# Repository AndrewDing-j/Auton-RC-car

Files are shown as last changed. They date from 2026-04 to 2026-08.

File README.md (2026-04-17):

# Auton-RC-car
## An autonomous car powered by Raspberry Pi 5 and Arduino Nano 33 BLE Sense which can navigate through roads of various width that are flanked by walls.

### Why this project?
I have always been interested in computer vision and found that this was a great excuse to make a project centred on that. Automation facinates me and I am very aware of how the world is rapidly moving towards self-driving vehicles through autonomous taxi services. I wanted to try my own hand in building something similar while also building the skills that could help me contribute to a better, more sustainable future.

### Software:
The Raspberry Pi is responsible for processing environmental data, while the Arduino serves as the controller for most peripherals, excluding the camera, and handles IMU information.
Uses a simple command protocol which allows the Arduino and Raspberry Pi to communicate with one another and interpret several commands.

### Hardware:
The chassis is that of a WL Toys K989 1:28 Scale Rally Car. All components - except for the suspension springs, wheels, bumper, and a majority of the steering mechanism - have been removed or replaced with 3DP parts.





**Current main features include:**
---------------------------------------------------------------------
- **Auckerman Steering** (Comes as a part of the chassis and I could not find the details that would allow me to make a CAD of it)
- - Enables sharper turns
- - Smoother steering
- - Greater control at low speeds
- - Reduced tire scrubbing
- **Wide-angle Pi 5 Camera (CSI interface, 130+ FOV)**
- - Wide FOV for wall detection
- - Inexpensive, so easily replacable
- - 4K resolution
- **Raspberry Pi 5**
- - Handles visual data from camera
- - Processes visual information with the help of a Python script utilizing OpenCV
- - Reacts to the environment and sends commands to an Arduino Nano based on the data recieved
- - Generally handles driving in two states: "STRAIGHT" and "TURN"
- **Yahboom PSU Expansion Board for Raspberry Pi 5**
- - Provides stable power to Raspberry Pi 5
- - Indirectly powers Arduino Nano through Raspberry Pi 5
- - Supplied with a 2 cell 1300mAh LiPo Gens Ace battery
- **Arduino Nano 33 BLE Sense**
- - Compact
- - Controls motors and servos
- - Returns IMU gyroscopic data
- - Runs callibration script to counteract the IMU's gyroscopic drift
- - Handles commands



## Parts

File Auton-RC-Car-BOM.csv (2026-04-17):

Item | Quantity | Description
WL Toys K989 1:28 Scale Rally Car (RTR) | 1 | Contains aluminum 1:28 sclae RC car chassis. Wheels attached.
8MP Camera for Raspberry Pi 5 IMX219 130° FOV CSI Interface with 15 cm FFC for RPI 5 Zero/ZeroW/2W | 1 | 130 Degree wide camera with 8MP/4K resolution. Captures visual information so the Raspberry Pi 5 can send appropriate commands to the Arduino module.
Yahboom Power supply Expansion Board for Raspberry Pi 5 (5V/5A, ideally USB PD power supply) | 1 | Provides a regulated 5.0V source of power to the Raspberry Pi 5.
LiPo battery | 1 | Rechargeable Gens Ace 2 cell 1300mAh 7.4v battery with a female dean connector. Serves as the main power source.
Button (to start the robot) | 1 | Button to power the RC Car on and off.
Arduino Nano 33 BLE Sense Rev2 | 1 | Arduino Nano module with an on board IMU. Requires 3.3v power supply. Will control the peripheries which move the RC Car
Hitec HS-5055MG Servo Motor | 1 | 11.9g metal gear digital microservo. Steers the car and controlled by the Arduino module through the Lizard Pro Esc.
Furitek Lizard Pro 30A/50A Brushed/Brushless Esc For Axial SCX24 With FOC Technology | 1 | Esc with controls for BLDC motor and servo. Can recieve and redistribute power.
BLDC Motor | 1 | 17.5g BLDC micro motor with an rpm of 3450/KV. Will provide speed for the motor and controlled through the Esc.
Main Platform | 1 | 3DP platform with holes for the Arduino, Raspberry Pi, and other 3DP components.
Battery Mount | 1 | 3DP Platform to maintain the LiPo battery in a central area.
Camera Mount | 1 | 3DP frame structure with holes drilled at the top to screw on the 8MP Camera. Attaches to the Raspberry Pi 5 with pegs.
Motor Holder/Gearbox | 1 | 3DP gerabox that keeps the BLDC motor stable and in place.
Wheel Clamp | 2 | 3DP piece that keeps suspensions springs and bottom of wheels from going above the chassis.
Steering Rod | 1 | 3DP steering rod attached to the wheels and servo.

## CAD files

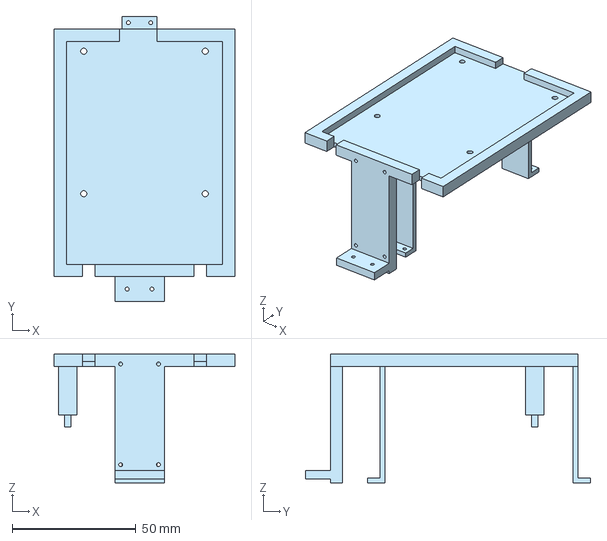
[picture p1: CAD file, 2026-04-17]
3DP/Main Platform.step
73.0 x 115.0 x 52.0 mm

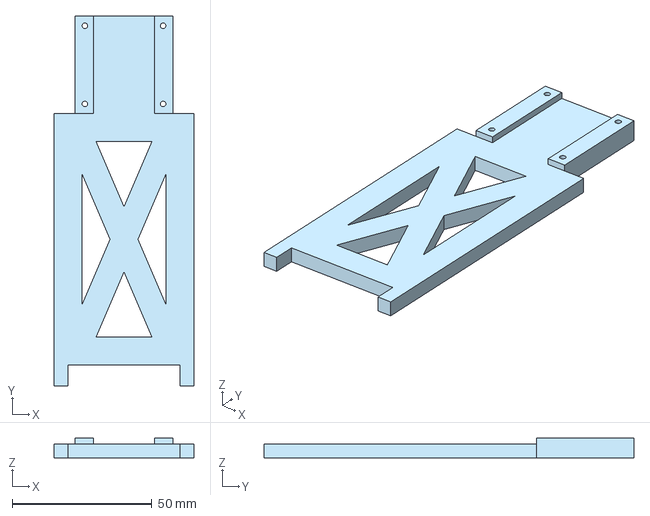
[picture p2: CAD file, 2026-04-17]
3DP/Camera Mount.step
50.0 x 132.5 x 7.10 mm

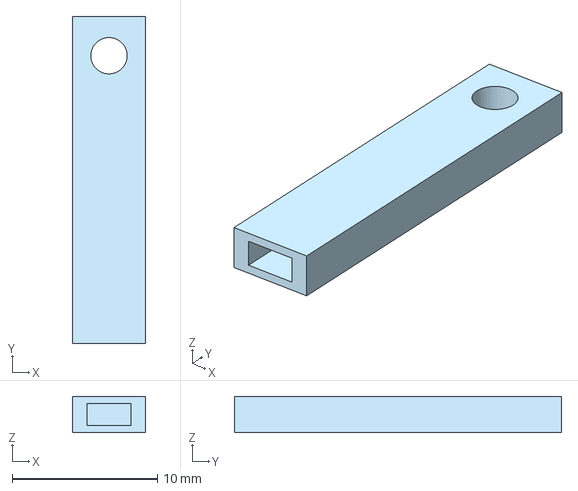
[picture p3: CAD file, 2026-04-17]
3DP/Bottom part 1.step
5.00 x 22.5 x 2.50 mm

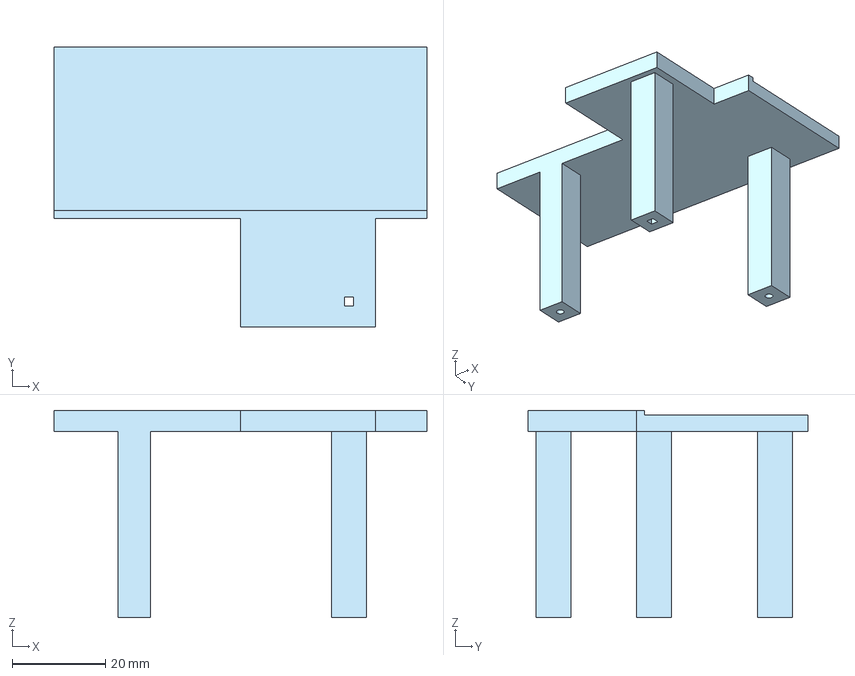
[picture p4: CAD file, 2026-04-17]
3DP/Battery Mount.step
80.0 x 60.0 x 44.5 mm

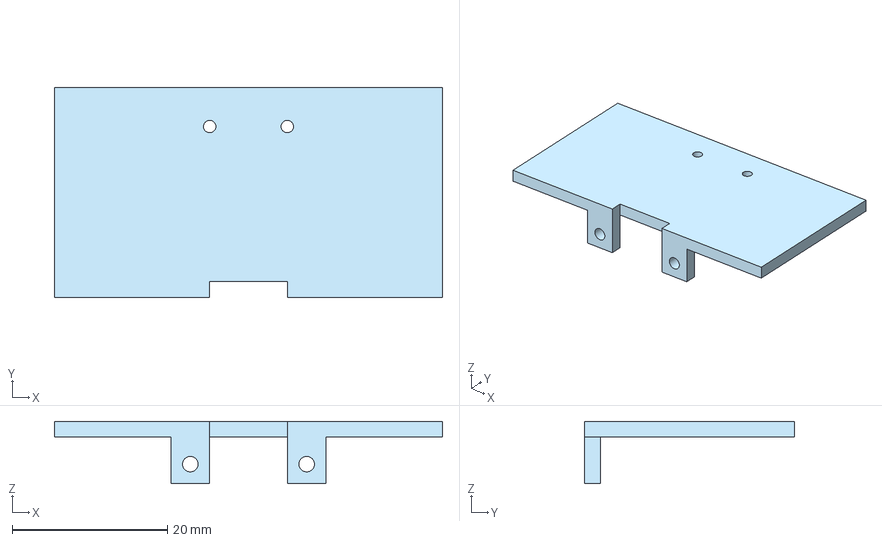
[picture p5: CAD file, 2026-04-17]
3DP/Wheel clamp.step
50.0 x 27.0 x 8.00 mm

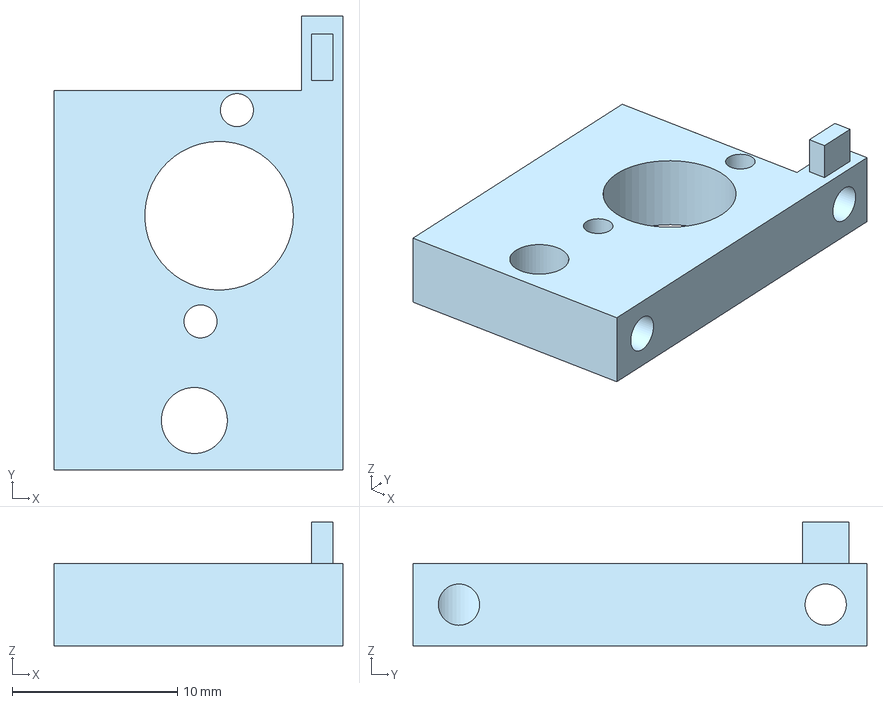
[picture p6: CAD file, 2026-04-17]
3DP/Gearbox.step
17.5 x 27.5 x 7.50 mm

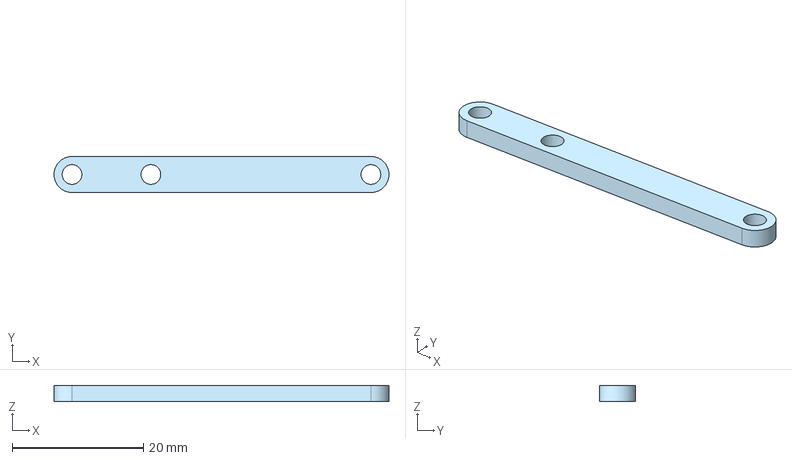
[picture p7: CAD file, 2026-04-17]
3DP/Steering Rod.step
51.0 x 5.50 x 2.50 mm

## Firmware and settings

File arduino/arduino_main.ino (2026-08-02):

#include <Arduino.h>
#include <ctype.h>
#include <string.h>
#include <stdlib.h>
#include <Servo.h>
#include <Arduino_BMI270_BMM150.h>

static float q0=1, q1=0, q2=0, q3=0;
static float eIx=0, eIy=0, eIz=0;
static unsigned long lastTime = 0;
static float gbx=0, gby=0, gbz=0;

// reference quaternion everything is relative to this after zeroing
static float r0=1, r1=0, r2=0, r3=0;

// cached mag updated only when new data arrives, used every frame
static float cachedMx=0, cachedMy=0, cachedMz=0;

static const size_t MAX_LINE = 16;  // Max command line length, excluding EOL
static char lineBuf[MAX_LINE + 1];
static size_t lineLen = 0;
static const char SOC = '$';  // start of command character
static bool inCommand = false;
static float biasX = 0.0, biasY = 0.0, biasZ = 0.0;
Servo servo;
Servo motor;
#define SERVO_PIN 8
#define MOTOR_PIN 9

// This need to be calibrated board to board. Please uncomment calibrateMag() under void loop to do so.
#define MAG_X_OFFSET  39.0f
#define MAG_Y_OFFSET  30.0f
#define MAG_Z_OFFSET  13.5f

// Kp = how fast it corrects, Ki = slowly kills gyro bias
#define Kp  2.0f
#define Ki  0.05f

static float heading = 0.0f;

void calibrateGyro() {
  Serial.println("Keep still — calibrating gyro...");
  float sx=0, sy=0, sz=0;
  int n = 2000;
  for (int i=0; i<n; i++) {
    float gx,gy,gz;
    while (!IMU.gyroscopeAvailable());
    IMU.readGyroscope(gx,gy,gz);
    sx+=gx; sy+=gy; sz+=gz;
    delay(3);
  }
  gbx=sx/n; gby=sy/n; gbz=sz/n;
  Serial.print("Gyro bias: ");
  Serial.print(gbx,4); Serial.print(" ");
  Serial.print(gby,4); Serial.print(" ");
  Serial.println(gbz,4);
}

// run once, rotate board in all directions 30s, paste offsets above
void calibrateMag() {
  Serial.println("Rotate board in all directions for 30s...");
  float xmin=1e9,xmax=-1e9,ymin=1e9,ymax=-1e9,zmin=1e9,zmax=-1e9;
  unsigned long start = millis();
  while (millis()-start < 30000) {
    if (!IMU.magneticFieldAvailable()) continue;
    float mx,my,mz;
    IMU.readMagneticField(mx,my,mz);
    xmin=min(xmin,mx); xmax=max(xmax,mx);
    ymin=min(ymin,my); ymax=max(ymax,my);
    zmin=min(zmin,mz); zmax=max(zmax,mz);
    delay(10);
  }
  Serial.println("Done! Paste these into your #defines:");
  Serial.print("#define MAG_X_OFFSET  "); Serial.println((xmin+xmax)/2, 4);
  Serial.print("#define MAG_Y_OFFSET  "); Serial.println((ymin+ymax)/2, 4);
  Serial.print("#define MAG_Z_OFFSET  "); Serial.println((zmin+zmax)/2, 4);
  while(1);
}

void mahonyUpdate(float ax, float ay, float az,
                  float gx, float gy, float gz,
                  float mx, float my, float mz, float dt) {
  float norm;

  norm = sqrtf(ax*ax+ay*ay+az*az);
  if (norm == 0) return;
  ax/=norm; ay/=norm; az/=norm;

  norm = sqrtf(mx*mx+my*my+mz*mz);
  if (norm == 0) return;
  mx/=norm; my/=norm; mz/=norm;

  float hx = 2*(mx*(0.5f-q2*q2-q3*q3) + my*(q1*q2-q0*q3) + mz*(q1*q3+q0*q2));
  float hy = 2*(mx*(q1*q2+q0*q3) + my*(0.5f-q1*q1-q3*q3) + mz*(q2*q3-q0*q1));
  float bx = sqrtf(hx*hx+hy*hy);
  float bz = 2*(mx*(q1*q3-q0*q2) + my*(q2*q3+q0*q1) + mz*(0.5f-q1*q1-q2*q2));

  float vx = 2*(q1*q3-q0*q2);
  float vy = 2*(q0*q1+q2*q3);
  float vz = q0*q0-q1*q1-q2*q2+q3*q3;
  float wx = 2*(bx*(0.5f-q2*q2-q3*q3) + bz*(q1*q3-q0*q2));
  float wy = 2*(bx*(q1*q2-q0*q3)       + bz*(q0*q1+q2*q3));
  float wz = 2*(bx*(q0*q2+q1*q3)       + bz*(0.5f-q1*q1-q2*q2));

  float ex = (ay*vz-az*vy) + (my*wz-mz*wy);
  float ey = (az*vx-ax*vz) + (mz*wx-mx*wz);
  float ez = (ax*vy-ay*vx) + (mx*wy-my*wx);

  eIx += Ki*ex*dt;
  eIy += Ki*ey*dt;
  eIz += Ki*ez*dt;

  gx += Kp*ex + eIx;
  gy += Kp*ey + eIy;
  gz += Kp*ez + eIz;

  gx *= DEG_TO_RAD;
  gy *= DEG_TO_RAD;
  gz *= DEG_TO_RAD;

  float dq0 = 0.5f*(-q1*gx-q2*gy-q3*gz)*dt;
  float dq1 = 0.5f*( q0*gx+q2*gz-q3*gy)*dt;
  float dq2 = 0.5f*( q0*gy-q1*gz+q3*gx)*dt;
  float dq3 = 0.5f*( q0*gz+q1*gy-q2*gx)*dt;

  q0+=dq0; q1+=dq1; q2+=dq2; q3+=dq3;

  norm = sqrtf(q0*q0+q1*q1+q2*q2+q3*q3);
  q0/=norm; q1/=norm; q2/=norm; q3/=norm;
}

void readAndFuse(float dt) {
  // update mag cache only when fresh data is ready (it's slow ~10Hz)
  if (IMU.magneticFieldAvailable()) {
    float mx,my,mz;
    IMU.readMagneticField(mx,my,mz);
    // BMI270 rotated 90deg on board + align to same frame
    cachedMx =  my - MAG_X_OFFSET;
    cachedMy = -mx - MAG_Y_OFFSET;
    cachedMz = -mz - MAG_Z_OFFSET;
  }

  // always run filter at full speed with last known mag
  if (!IMU.accelerationAvailable() || !IMU.gyroscopeAvailable()) return;

  float ax,ay,az,gx,gy,gz;
  IMU.readAcceleration(ax,ay,az);
  IMU.readGyroscope(gx,gy,gz);
  gx -= gbx; gy -= gby; gz -= gbz;

  float rax=-ax, ray=ay, raz=az;
  float rgx=-gx, rgy=gy, rgz=gz;

  mahonyUpdate(rax,ray,raz, rgx,rgy,rgz, cachedMx,cachedMy,cachedMz, dt);
}

void warmupAndZero() {
  Serial.println("Warming up — keep still...");

  // seed the mag cache before warmup starts
  while (!IMU.magneticFieldAvailable());
  float mx,my,mz;
  IMU.readMagneticField(mx,my,mz);
  cachedMx =  my - MAG_X_OFFSET;
  cachedMy = -mx - MAG_Y_OFFSET;
  cachedMz = -mz - MAG_Z_OFFSET;

  unsigned long start = millis();
  lastTime = micros();
  while (millis()-start < 3000) {
    unsigned long now = micros();
    float dt = (now-lastTime)*1e-6f;
    if (dt < 0.002f) continue;
    lastTime = now;
    if (dt > 0.05f) dt = 0.05f;
    readAndFuse(dt);
  }

  // store inverse of settled quaternion so all angles are relative to startup pose
  r0= q0; r1=-q1; r2=-q2; r3=-q3;
  Serial.println("Zeroed. Go!");
}

void startupCalibration() {
  calibrateGyro();
  warmupAndZero();
  lastTime = micros();
  heading = 0.0f;
}

static void processCommand(char* cmd, float heading=heading) {
  if (!cmd || cmd[0] == '\0') return;

  char* cr = strchr(cmd, '\r');
  if (cr) *cr = '\0';

  while (*cmd && isspace((unsigned char)*cmd)) cmd++;  // Trim leading whitespace
  if (*cmd == '\0') return;

  char type = *cmd++;

  // Parse int argument
  char* endp = nullptr;
  long val = strtol(cmd, &endp, 10);

  if (type == 'C') {  // (re-)calibrate gyro and zero heading
      startupCalibration();
  } else if (type == 'S') {                            // Set servo position
      if (val < 25 || val > 130) return;  // Invalid angle
      //Serial.println(val);
      servo.write(val);
  } else if (type == 'M') {  // return IMU data and turn
    if (val < 1000 || val > 2000) return;  // Invalid speed
    motor.writeMicroseconds(val);
    //Serial.println(val);
  } else if (type == 'L') {
    if (val < 22 || val > 24) return;  // Invalid LED
    digitalWrite(22, LOW);
    digitalWrite(23, LOW);
    digitalWrite(24, LOW);
    digitalWrite(val, HIGH);
  } else if (type == 'I') {
    Serial.println(heading);
  }
}

void setup() {
  pinMode(22, OUTPUT); // blue
  pinMode(23, OUTPUT); // red
  pinMode(24, OUTPUT); // green

  servo.attach(SERVO_PIN, 900, 2100);
  motor.attach(MOTOR_PIN, 1000, 2000);
  servo.write(80);
  motor.writeMicroseconds(1500);

  Serial.begin(115200);
  while (!Serial);

  if (!IMU.begin()) {
    Serial.println("Failed to initialize IMU!");
    while (1);
  }
  Serial.println("IMU initialized successfully.");

  // uncomment once to get mag offsets, paste above, then comment out again
  //calibrateMag();

  startupCalibration();
}

void loop() {
  // CMD Processing
  if (Serial.available() > 0) {
    char c = (char)Serial.read();
    if (c == SOC) {
      inCommand = true;
      lineLen = 0;
    }
    else if (inCommand) {
      if (c == '\n') {
        lineBuf[lineLen] = '\0';  // Null-terminate command
        processCommand(lineBuf, heading);
        inCommand = false;
        lineLen = 0;
      } else if (lineLen < MAX_LINE) {
        lineBuf[lineLen++] = c;  // Append char to command buffer
      } else {
        // Command too long
        inCommand = false;
        lineLen = 0;
      }
    }
  }

  //IMU Background Processing
  if (IMU.gyroscopeAvailable()) {
    float x, y, z;
    IMU.readGyroscope(x, y, z);
    z -= gbz;

    if (abs(z) < 0.1) z = 0.0;  // ignores insignificant gyro readings/noise
      
    unsigned long now = micros();
    float dt = (now-lastTime)*1e-6f;  // calc dt (elapsed time)
    lastTime = now;

    heading -= dt * z;  // integrate gyro's angular velocity to get heading
  }
}

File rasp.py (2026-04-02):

import time, serial, cv2, numpy as np
from picamera import PiCamera
from time import sleep

# Camera init
picam2 = PiCamera()
picam2.preview_configuration.main.size = (640, 480)
picam2.preview_configuration.main.format = "RGB888"
picam2.preview_configuration.controls.FrameRate = 30
picam2.preview_configuration.align()
picam2.configure("preview")
picam2.start()
sleep(2) # Let the camera warm up

ser = serial.Serial('/dev/ttyACM0', 112500, timeout=1) # Update with your Arduino's port
ser.reset_input_buffer() # Clear any pending data
ser.reset_output_buffer()

# Define ROIs (x1, y1, x2, y2)
roi1 = [20, 170, 240, 220] # Left side
roi2 = [400, 170, 620, 220] # Right side

def drawRoi(img, roi, color=(0, 255, 0), thickness=2, label=None):
    # Draws a rectangle on the image to indicate the ROI.
    x1, y1, x2, y2 = roi
    cv2.rectangle(img, (x1, y1), (x2, y2), color, thickness)
    if label:
        cv2.putText(img, label, (x1, max(15, y1 - 8)), 
                    cv2.FONT_HERSHEY_SIMPLEX, 1, color, 2, cv2.LINE_AA)
    return img

def wallAreaLab(frameRgb, roi, LabLower, LabUpper, minContour = 50):
    # Calculate percentage of pixels withing the Lab range in the ROI
    x1, y1, x2, y2 = roi
    roiImg = frameRgb[y1:y2, x1:x2]
    roiLab = cv2.cvtColor(roiImg, cv2.COLOR_RGB2Lab)
    roiLab = cv2.GaussianBlur(roiLab, (7,7), 0) # larger kernel = more smoothing
    mask = cv2.inRange(roiLab, LabLower, LabUpper)

    #noice cleanup
    kernel = np.ones((5,5), np.uint8)
    mask = cv2.morphologyEx(mask, cv2.MORPH_OPEN, kernel, iterations=1)
    mask = cv2.morphologyEx(mask, cv2.MORH_CLOSE, kernel, iterations=2)

    contours, _ = cv2.findContours(mask, cv2.RETR_EXTERNAL, cv2.CHAIN_APPROX_SIMPLE)
    areaMax = 0
    contourMax = None
    for c in contours:
        area = cv2.contourArea(c)
        if area >= minContour and area > areaMax:
            areamax = area
            contourMax = c
    if contourMax is not None:
        contourMax += [x1, y1] #shift contour points to full-frame coordinates
    return areaMax, contourMax, mask

def pidController(error, prevError, kp=0.1, ki=0.01, kd=0.05):
    global integral, prevError
    integral += error
    correction = kp * error + ki * integral + kd * (error - prevError)
    prevError = error
    return correction

# Define thresholds
LAB_LOWER = np.array([20,120,120], dtype=np.uint8) #adjust LAB_LOWER and LAB_UPPER based on the wall colour
LAB_UPPER = np.array([70,255,255], dtype=np.uint8)
ENTER_TURN_THRESH = 550
EXIT_TURN_THRESH = 1200
EXIT_TIME_THRESH = 5.0
EXIT_ANGLE_THRESH = 85.0

# Trigger protection
CONFRIM_FRAMES = 5  # Number of consecutive frames required to confirm a turn
side = None
confirmCount = 0
turnTime = None

# Turning variables
enterTurnDegree = None
turningDegree = None
turnsCompleted = 0

# PID variables
prevError = 0
integral = 0

mode = "STRAIGHT" #STRAIGHT, TURNING

# --- Main loop --- #
while True:
    frame = picam2.capture_array()
    now = time.monotonic()

    leftContour, leftMask, leftArea = wallAreaLab(frame, roi1, LAB_LOWER, LAB_UPPER)
    rightContour, rightMask, rightArea = wallAreaLab(frame, roi2, LAB_LOWER, LAB_UPPER)

    # --- State Machine --- #
    if mode == "STRAIGHT":
        ser.write(f"$S{pidController(leftArea-rightArea)}\n")
        if leftArea < ENTER_TURN_THRESH or rightArea < ENTER_TURN_THRESH:
            confirmCount += 1
        else:
            confirmCount = 0
        
        if confirmCount >= CONFIRM_FRAMES:
            if leftArea < rightArea:
                side = "LEFT"
            else:
                side = "RIGHT"
            confirmCount = 0
            mode = "TURNING"
            turnTime = now
            enterTurnDegree = int(ser.readline().decode().strip()) # Read current degree from Arduino's IMU
    
    elif mode == "TURNING":
        delta = abs(enterTurnDegree - int(ser.readline().decode()).strip())
        turningDegree = min(delta, 360 - delta) # handling of wrapping from 0 to 360 degrees
        elapsed = now - (turnTime if turnTime else now)
        if elasped > EXIT_TIME_THRESH and turningDegree > EXIT_ANGLE_THRESH:
            if (leftArea > EXIT_TURN_THRESH and side == "LEFT")\
                or (rightArea > EXIT_TURN_THRESH and side == "RIGHT"):
                mode = "STRAIGHT"
                side = None
                turnTime = None
                enterTurnDegree = None
                turningDegree = None
                turnsCompleted += 1
                continue
        ser.write(f"$T{leftArea-rightArea}\n") # negative result indicates "turn left" and vice versa

    # --- Visualization --- #
    drawRoi(frame, roi1, label="Left ROI")
    drawRoi(frame,roi2, label="Right ROI")

    #draw contours if found
    if leftContour:
        cv2.drawContours(frame, [leftContour], -1, (255, 0, 0), 2)
    if rightContour:
        cv2.drawContours(frame, [rightContour], -1, (255, 0, 0), 2)
    
    #numeric values for debugging
    cv2.putText(frame, f"Left Area: {leftArea}", (roi1[0], roi1[1]-40),
                cv2.FONT_HERSHEY_SIMPLEX, 1, (0, 255, 0), 2)
    cv2.putText(frame, f"Right Area: {rightArea}", (roi2[0], roi2[1]-40),
                cv2.FONT_HERSHEY_SIMPLEX, 1, (0, 255, 0), 2)
    cv2.putText(frame, f"Confirm Count: {confirmCount}", (roi1[0], 90),
                cv2.FONT_HERSHEY_SIMPLEX, 1, (0, 255, 0), 2)
    cv2.putText(frame, f"Elapsed Turning Time: {now - (turnTime if turnTime else now):.2f}s", (roi1[0], roi1[3]+30),
                cv2.FONT_HERSHEY_SIMPLEX, 1, (0, 255, 0), 2)
    cv2.putText(frame, f"Mode: {mode}", (roi1[0], 30),
                cv2.FONT_HERSHEY_SIMPLEX, 1, (0, 255, 0), 2)
    cv2.putText(frame, f"Side: {side}", (roi2[0], 30),
                cv2.FONT_HERSHEY_SIMPLEX, 1, (0, 255, 0), 2)
    
    #display frame
    cv2.imshow("Frame", frame)
    cv2.imshow("LeftMask", leftMask)
    cv2.imshow("RightMask", rightMask)

    if cv2.waitKey(1) & 0xFF == ord('q'):
        break
cv2.destroyAllWindows()
picam2.stop()

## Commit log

2026-03-22 Created python file for the raspberry pi and imported the base modules
2026-03-25 Added 3DP parts
    Parts for camera mounting, platforms for mounting the battery, Arduino Nano, and RaspberryPi. Wheel holder to provide extra stability to the chassis.
    [Battery & Arduino Mount.stl, Bottom Parts.stl, Camera Mount.stl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]
2026-03-28 Debugging displays for the raspberry Pi and camera
2026-03-28 Debbugging screens for the Raspberry Pi and Camera
2026-04-01 Beginning of development of PD controller for the Raspberry Pi 5.
    Gyro Calibration for the Nano's IMU complete.
2026-04-01 PID Controller v2
    straightDrive function and turning prototypes complete.
    Communications between Raspberry Pi and Arduino adjusted to fit the functions/methods.
2026-04-02 Form fix in arduino_main
    [arduino_main.ino]
2026-04-15 Updated 3D Models
    The wheel clamp, camera mount, and Raspberry Pi platform were all changed to fit better with the car's concept.
    [Camera Mount.stl, Raspberry Pi Platform.stl, Wheel clamp.stl]
2026-04-16 Added Model of the RC Car
    The most important parts to take note of are the 3DP elements, as there seem to be no good schematics of the chassis being used available. The wheels, axel, motor, and chassis itself are all rough ap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
2026-04-17 Rename Battery & Arduino Mount.stl to Battery Mount.stl
    [Battery Mount.stl]
2026-04-17 Updated Critical CAD
    Includes updated CAD for the Main Assembly of the RC Car, main platform, and wheel clamp. The main platform now has screw holes and proper positioning for the Arduino, which is reflected in the Main 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
    [Main Platform.stl, Wheel clamp.stl]
2026-04-17 Added BoM
    [Auton-RC-Car-BOM.csv]
2026-04-17 Prepare to replace 3DP Directory
    [Battery Mount.stl, Bottom Parts.stl, Camera Mount.stl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]
2026-04-17 Reuploaded 3DP components
    [Battery Mount.step, Bottom part 1.step, Camera Mount.step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]
2026-04-17 Uploaded model of car
    It is a .STL file because for some reason, the .STEP version of the file is over 4 times larger and cannot be uploaded.
